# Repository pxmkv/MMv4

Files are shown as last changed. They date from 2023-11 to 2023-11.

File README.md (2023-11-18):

# MMv4

MMv4 is the 4rd generation robot platform used to teach the IEEE Micromouse DeCal at UC Berkeley. It was designed with usability, manufacturability, size, and cost in mind.

## Setup

1. Follow the assembly instructions in [lab1](docs/lab1.md) using the latest **BOM**.
2. Plug mouse into your computer and flash the Micropython firmware

## Labs

Skeleton lab code, lab documents, and solutions are stored in [labs/](labs/), [docs/](docs/), and [solutions/](solutions/), respectively. To get started with a lab, simply copy the contents of the folder over to the MicroPython drive and edit files from there.

* [sanity](docs/sanity.md) - Hardware Check
* [lab1](docs/lab1.md) - Assembly
* [lab2](docs/lab2.md) - MicroPython Basics
* [lab3](docs/lab3.md) - Encoders
* [lab4](docs/lab4.md) - IR Sensors and Gyroscope
* [lab5](docs/lab5.md) - Odometry, Gyroscope and Motor Control
* [lab6](docs/lab6.md) - Intro to PID
* [lab7](docs/lab7.md) - More PID
* [lab8](docs/lab8.md) - Maze Solving Primitives **(WIP)**

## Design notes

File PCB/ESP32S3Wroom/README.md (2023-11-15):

## This folder contains all design files of Micromouse with ESP32S3Wroom as MCU

**Software Used**
1. Altium Designer 22
2. AutoCAD 2022

**Parameter**
1. Vias hole size: 12mil~15mil
2. Vias diameter: 20mil~30mil
3. Tracks width: 10mil~30mil
4. Layers: 2 layers
5. Silkscreen width: 10mil
6. Copper thickness: 1oz

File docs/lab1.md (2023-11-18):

# Lab 1: CircuitPython Basics

## CircuitPython Basics

One of the most convenient features of CircuitPython is the ability to upload and modify code as if they were just files on a flash drive. Instead of editing code directly on the drive, we highly recommend **editing code locally** on your computer first and then copying it over to the drive to run. This reduces wear on the flash memory and ensures you have a local backup of your code.

On startup, CircuitPython looks for a file named `code.py` and runs it. There are a few differences, but for the most part it behaves just like normal Python. After uploading new code, you might need to bring up a serial monitor and press CTRL-C and CTRL-D to reload.

For debugging, the serial monitor is invaluable. This is where the output of `print` statements will go. You can even bring up a REPL. One important note is that you can't start an interactive session (e.g. `python -i code.py`) to further debug your code as CircuitPython will restart on entering one.

### Example 1: Blinky

Let's start with the blink example, the "Hello World" of embedded programming. Your mouse has a green LED on the Pi Pico and an onboard WS2812B NeoPixel RGB LED. Upload the following code to your mouse.

```python
import board     # pin definitions
import time      # time delay
import neopixel  # to control the WS2812B
import digitalio # to control the LED

print("Hello World!")

# setup the LED as an output
led = digitalio.DigitalInOut(board.LED)
led.direction = digitalio.Direction.OUTPUT

# setup the WS2812B
rgb = neopixel.NeoPixel(board.GP4, 1)

# blink
while True:
    rgb[0] = (255, 255, 255) # max brightness
    led.value = True
    time.sleep(0.5)
    rgb[0] = (0, 0, 0)
    led.value = False
    time.sleep(0.5)
```

Running the code, both LEDs should start blinking every 0.5s. Notice that before we start writing values to the LEDs, we need to set them up with the correct physical pin. Also, WS2812Bs can be chained into strings which is why we use `rgb[0]`, to address the first (and only) LED.

### Checkoff #1

1. Change something about the provided blink code such as RGB color and blink rate.

### Example 2: Unnecessarily Complex Blinky

Let's take a look at some more syntax. Upload the following code to your mouse.

```python
import board
import time
import neopixel

rgb = neopixel.NeoPixel(board.GP4, 1)

counter = 0
while True:
    counter += 1
    if counter % 5 == 0: # modulus a.k.a remainder
        rgb[0] = (100, 0, 0)
        time.sleep(0.5)
        rgb[0] = (0, 0, 0)
    else:
        for i in range(5): # 0, 1, 2, 3, 4
            time.sleep(0.1)
```

Here we introduce a couple programming constructs that are very common in coding. The `if` statement (pairable with `elif` and `else`) runs the block of code corresponding to the truthiness of what's next to the `if`. The `for` loop sequentially iterates through an object which in this case is `range(5)`.

### Checkoff #2

1. What is the blink pattern? How long is it on and off for?

### Example 3: 

Finally, let's test out the button on your mouse. It's connected to pin `GP3`. Fill in the TODOs below to have your RGB LED change color when the button is pressed.

```python
import board
import time
import neopixel
import digitalio

rgb = neopixel.NeoPixel(board.GP4, 1)

but = digitalio.DigitalInOut("""TODO which pin?""")
but.pull = digitalio.Pull.UP

while True:
    if but.value: # not pressed
        """TODO one color"""
    else: # pressed
        """TODO other color"""
```

### Checkoff #3

1. Demonstrate your working code.

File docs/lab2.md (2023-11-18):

# Lab 2: Assembly

PLUG YOUR PI PICO INTO YOUR COMPUTER BEFORE YOU SOLDER IT JUST TO MAKE SURE IT WORKS :D

## Assembly

Download the `ibom.html` from the [release](https://github.com/dragonlock2/MMv3/releases) that matches your board revision and open it in your preferred browser. The interactive BOM (bill of materials) shows what parts are needed on your mouse's PCB (printed circuit board) and where they need to be placed.

To see images of all parts, see the Google Drive link [here](https://drive.google.com/drive/folders/1rGae82BSrE_mvmMwKTBHT9P-unDKIKQj?usp=sharing).

Also check the latest release for any manufacturing notes to make an older board functionally equivalent to the newest revision.

### Reflow Soldering

Let's start with the back of the PCB which is where the majority of parts are located. Click `B` in the top right to show just the back.

<p align="center">
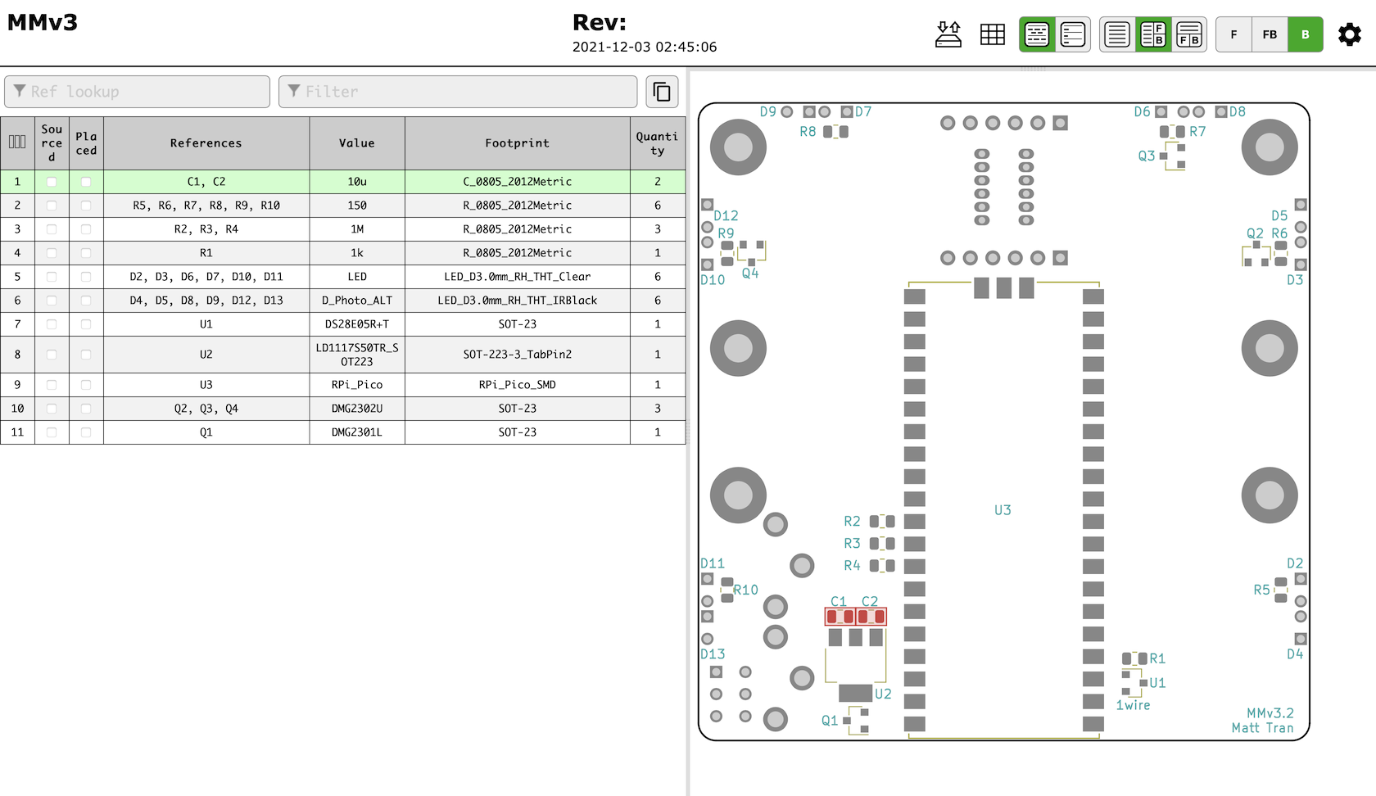
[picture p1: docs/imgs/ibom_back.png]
    
    <br>
    <a><b>iBOM Back</b></a>
</p>

Rather than solder each part by hand, we'll use reflow soldering which does it all at once. In reflow soldering, we place components on top of pads covered in solder paste before sending the whole thing through an oven to melt the solder, making permanent joints.

<p align="center">
    
    <br>
    <a><b>Reflow Solder Process</b></a>
</p>

Let's start by applying the solder paste using a **solder stencil**. Instead of squeezing the perfect amount onto each pad by hand, we can do it all at once by spreading paste over a stencil with holes cut out precisely where we want paste. For a good solder paste application, it's important to make sure the stencil is flush against the PCB and stays aligned. The process is very forgiving, so don't worry if your paste looks messy or goes a bit outside the pads.

<p align="center">
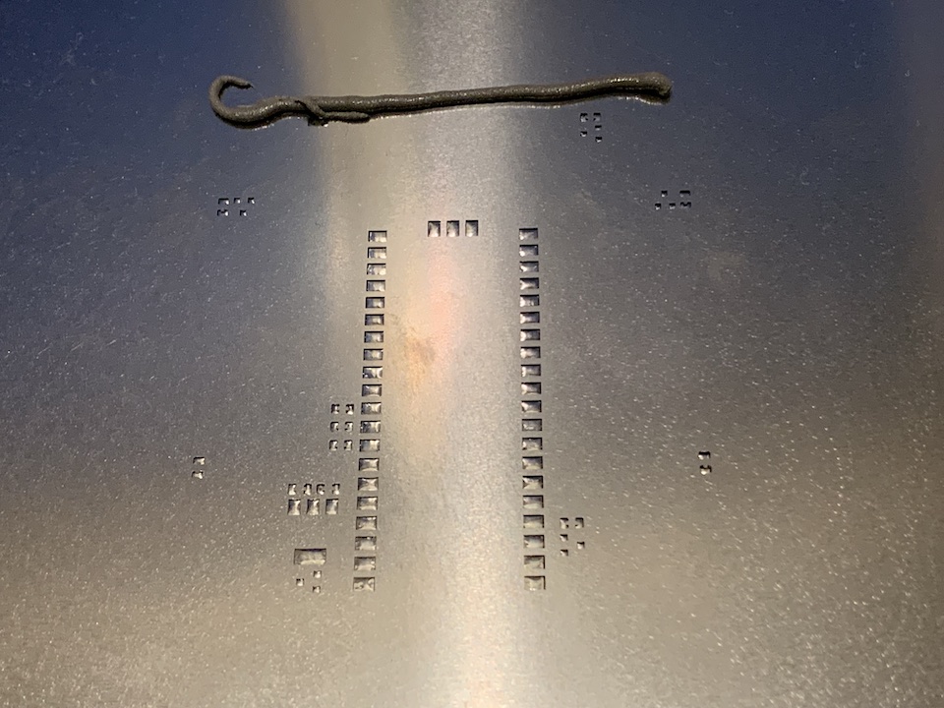
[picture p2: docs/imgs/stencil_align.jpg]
    
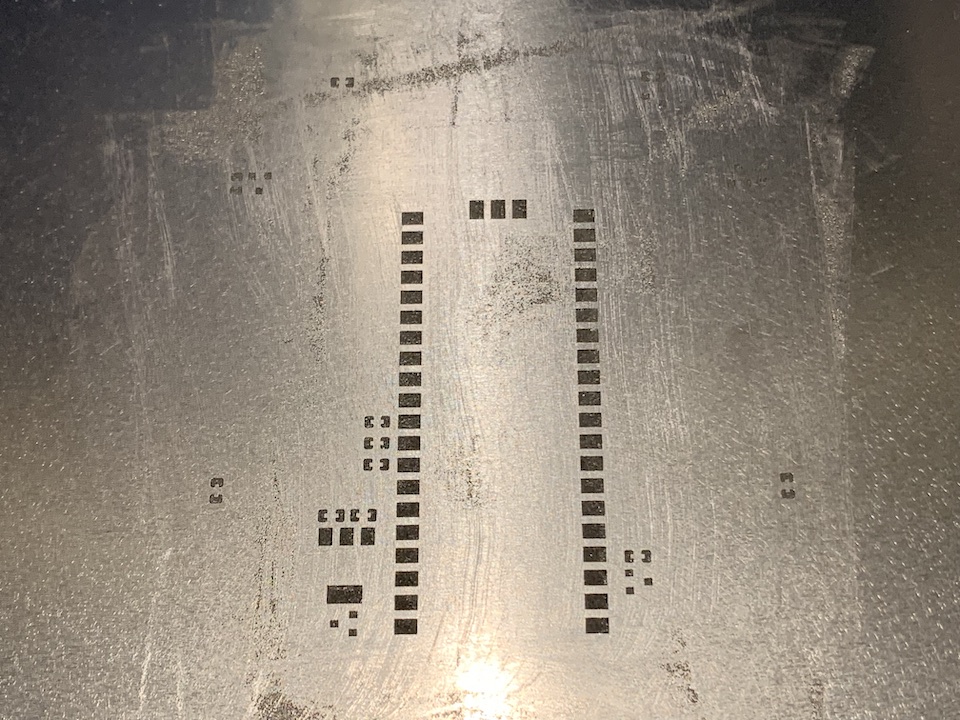
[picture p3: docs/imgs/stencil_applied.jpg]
    
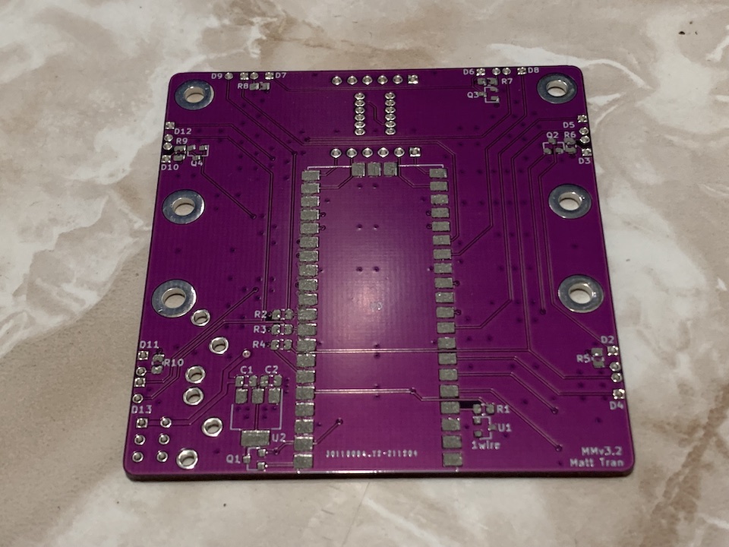
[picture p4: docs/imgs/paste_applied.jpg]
    
    <br>
    <a><b>Solder Paste Application Process</b></a>
</p>

Now it's time for component placement. Following the `ibom.html`, place all of the components for the back side. None of the symmetric components have polarity, so don't worry about part orientation. Tweezers will be very useful, but don't squeeze too hard or your component will go flying. When placing components, press down gently so that it digs into the paste a bit to prevent it from moving. Again, the process is quite forgiving so don't worry if your parts aren't perfectly aligned as solder surface tension will generally pull them into alignment.

<p align="center">
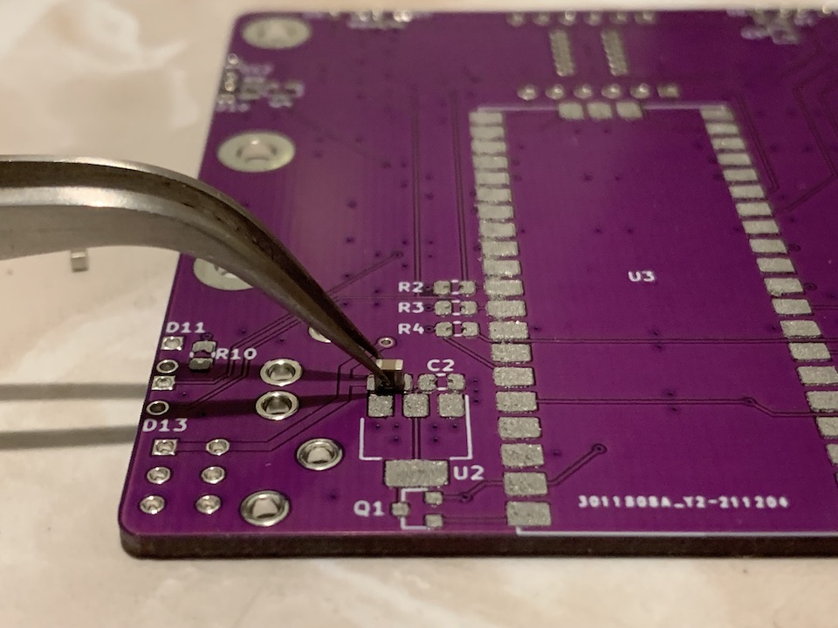
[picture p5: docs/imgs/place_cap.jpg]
    
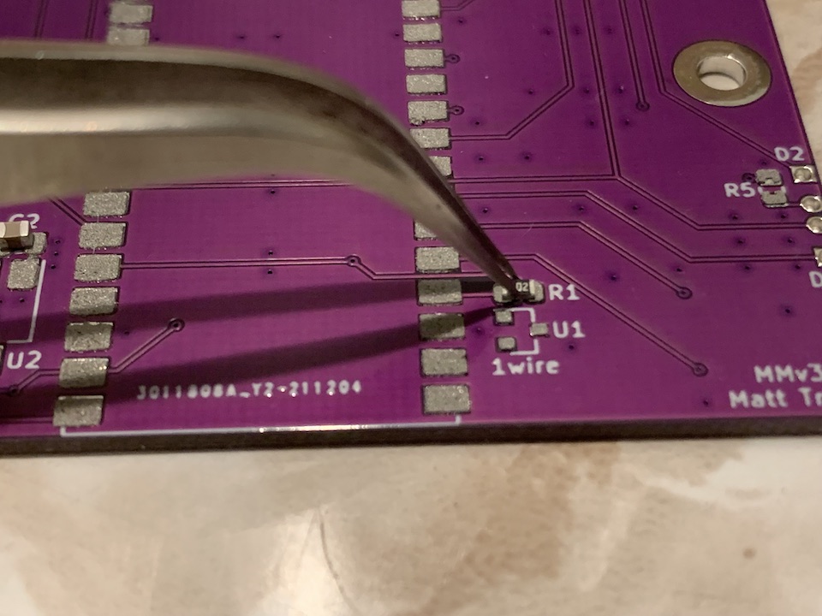
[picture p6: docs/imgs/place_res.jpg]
    
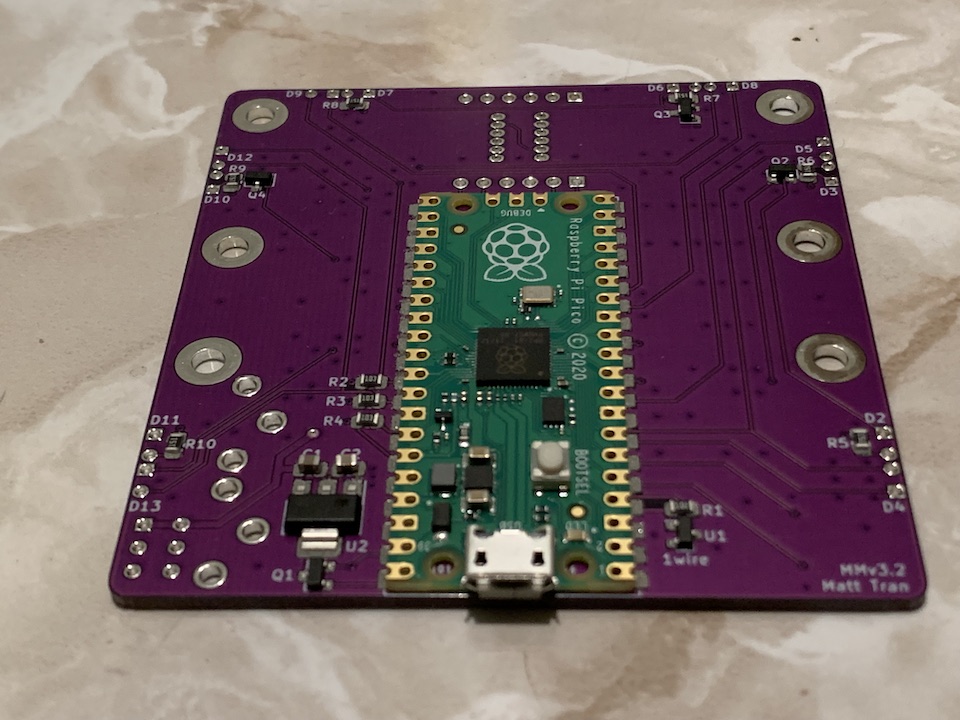
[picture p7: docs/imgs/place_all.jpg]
    
    <br>
    <a><b>Component Placement</b></a>
</p>

Finally, let's reflow the solder! Throw your board into the reflow oven, load up the correct profile, and wait. With any luck, all of your joints will melt and the back side of your board will be done.

<p align="center">
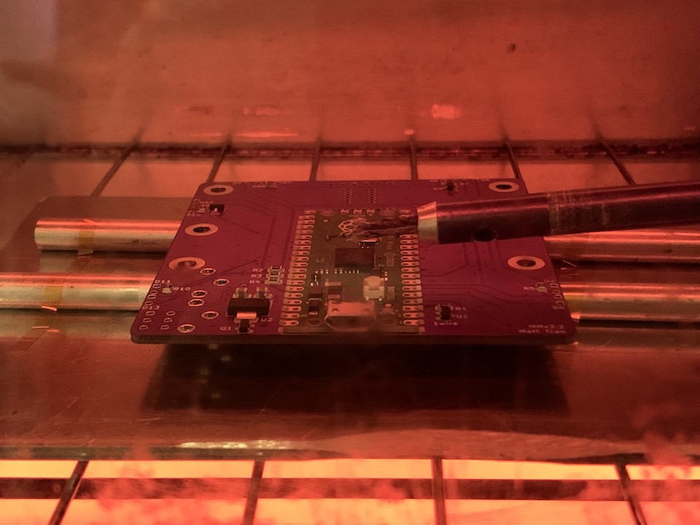
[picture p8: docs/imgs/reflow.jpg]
    
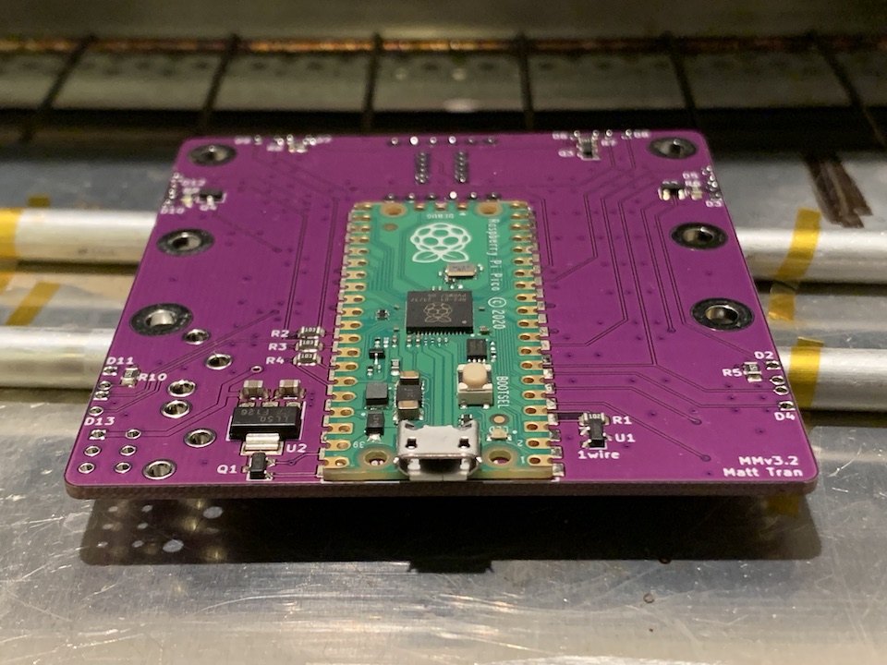
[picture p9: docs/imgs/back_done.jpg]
    
    <br>
    <a><b>Reflow</b></a>
</p>

### Hand Soldering

The rest of the components need to be attached by hand. The general process is to heat up both the pad and the part before melting solder onto both of them. Adafruit has a great list of common issues and fixes which can be found [here](https://learn.adafruit.com/adafruit-guide-excellent-soldering/common-problems).  

<p align="center">
    
    <br>
    <a><b>How to Make a Solder Joint</b></a>
</p>

Let's start with the DRV8833 motor driver board. Solder the two 6-pin headers onto the board and bridge the `en` pads as shown in the following pictures. The technique that I find works best is to solder just one pin first with the part in any orientation. Then reheat that joint while pressing on the part to move it into perfect alignment. Finally, do the rest of the pins.

<p align="center">
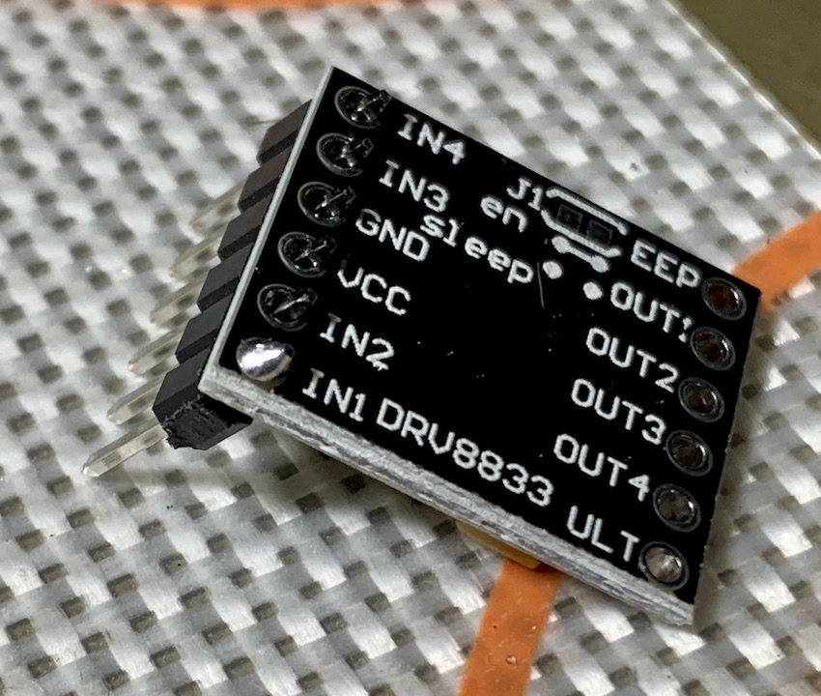
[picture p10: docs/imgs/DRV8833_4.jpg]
    
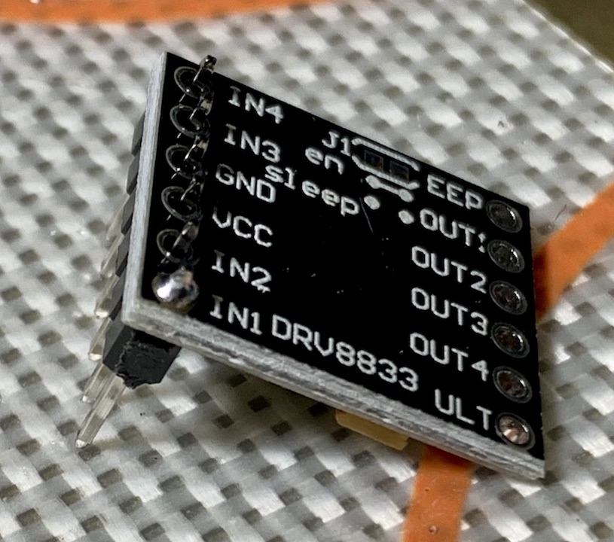
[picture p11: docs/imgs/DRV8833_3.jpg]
    
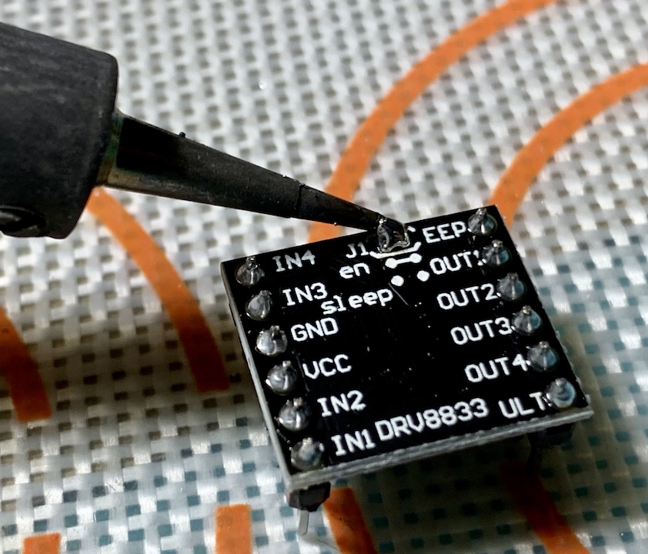
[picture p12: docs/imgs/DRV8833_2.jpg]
    
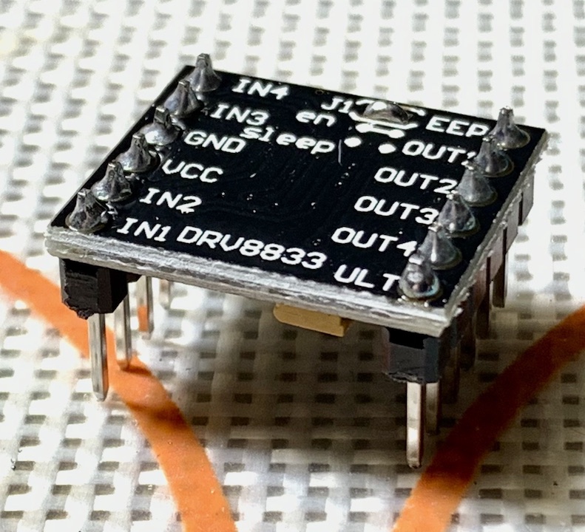
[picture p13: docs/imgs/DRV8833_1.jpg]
    
    <br>
    <a><b>DRV8833 Motor Driver Assembly</b></a>
</p>

Next let's finish off the mouse's main PCB. Click `F` in the `ibom.html` to see the remaining components.

<p align="center">
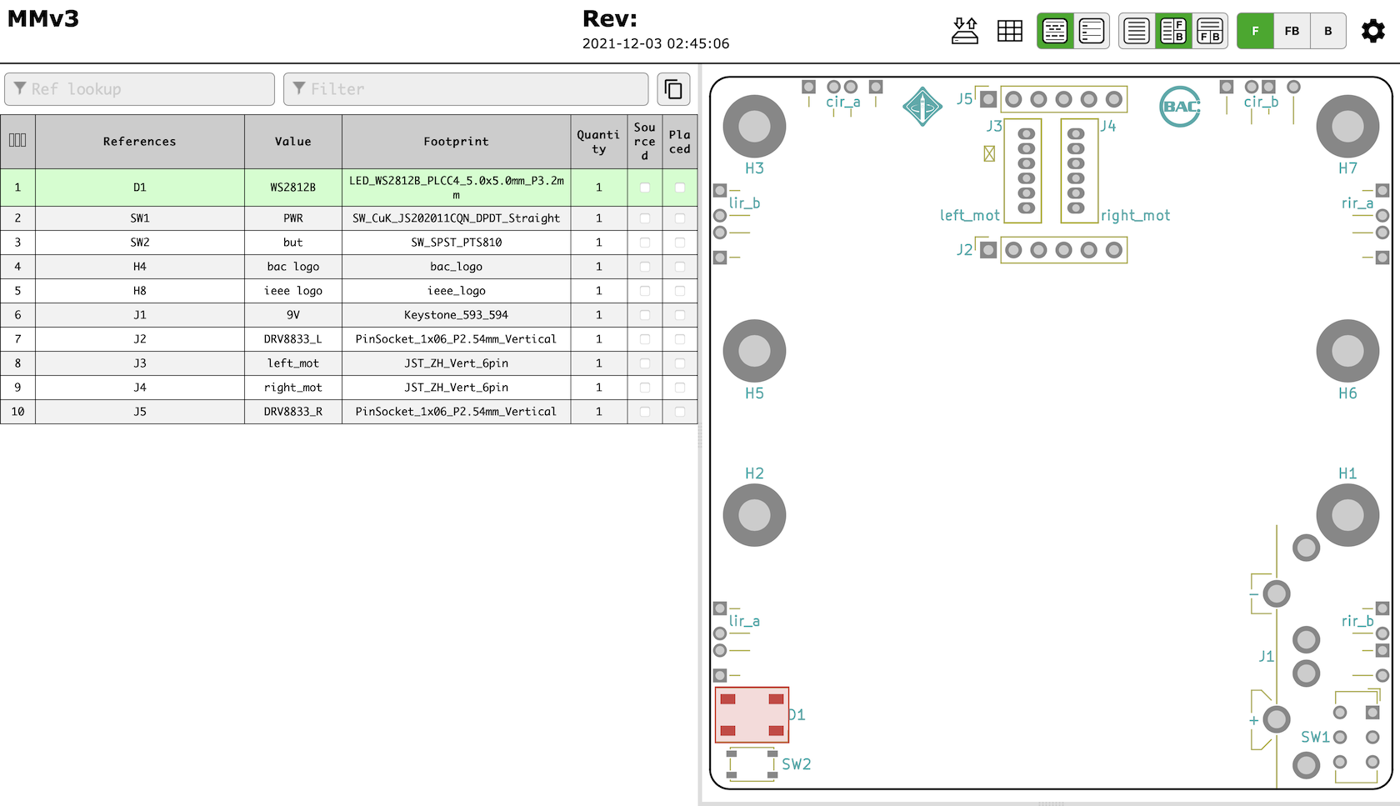
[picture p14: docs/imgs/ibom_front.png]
    
    <br>
    <a><b>iBOM Front</b></a>
</p>

To make alignment easier, starting with the shortest components usually works out best. The SMD components use the same soldering process except there's no hole to stick the part through. Some of the parts do have polarity, so if you're unsure make sure to ask your mentor.

<p align="center">
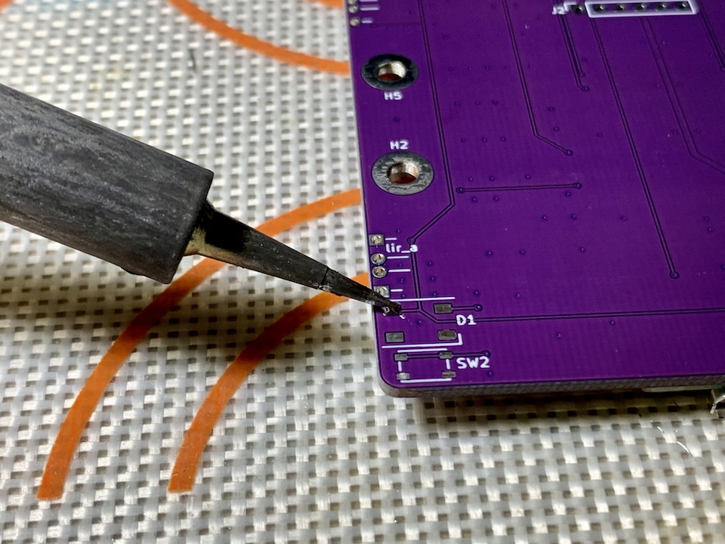
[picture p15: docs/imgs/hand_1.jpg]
    
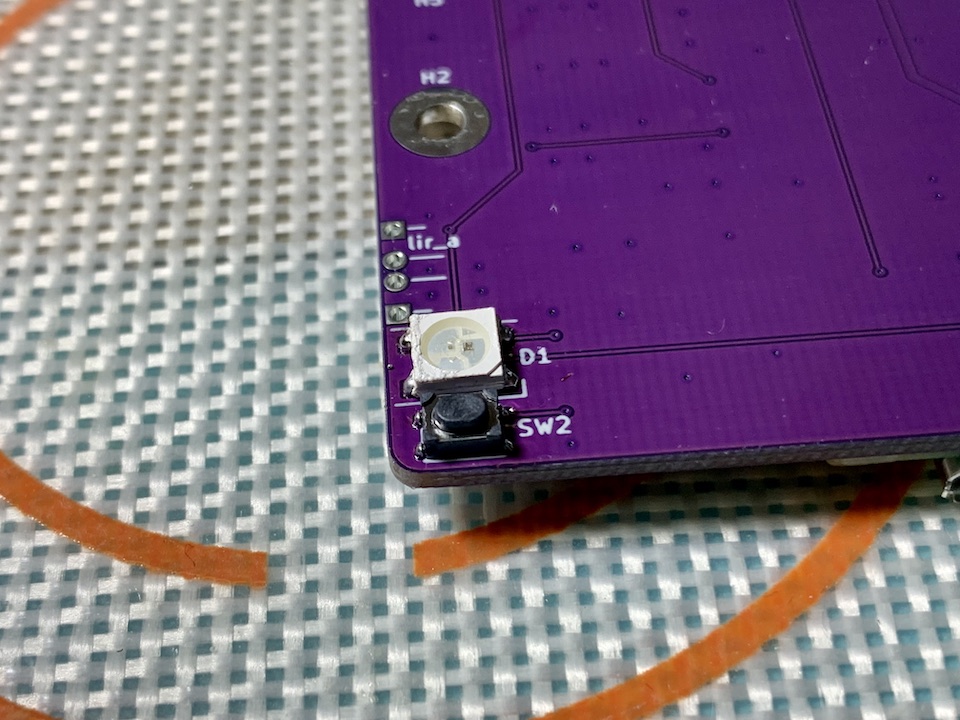
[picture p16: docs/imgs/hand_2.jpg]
    
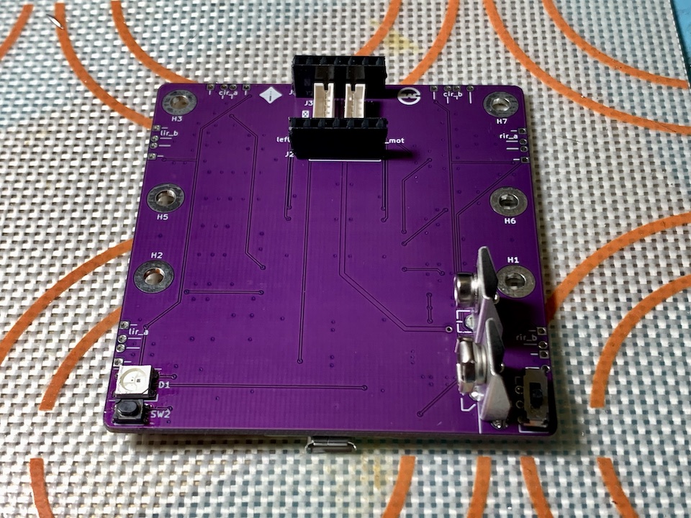
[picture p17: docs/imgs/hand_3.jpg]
    
    <br>
    <a><b>Some THT Components</b></a>
</p>

For the IR LEDs, the silkscreen should denote the polarity. They also need to be mounted at a right angle so don't be afraid to bend them. Splaying the leads outward should hold them in place while you apply solder.

<p align="center">
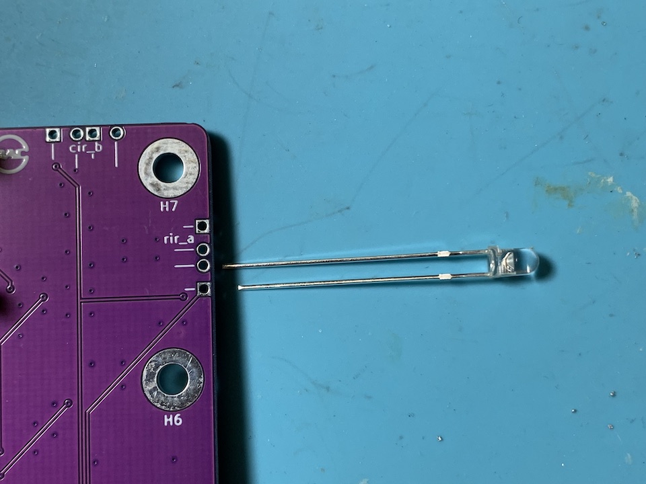
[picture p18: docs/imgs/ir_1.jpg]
    
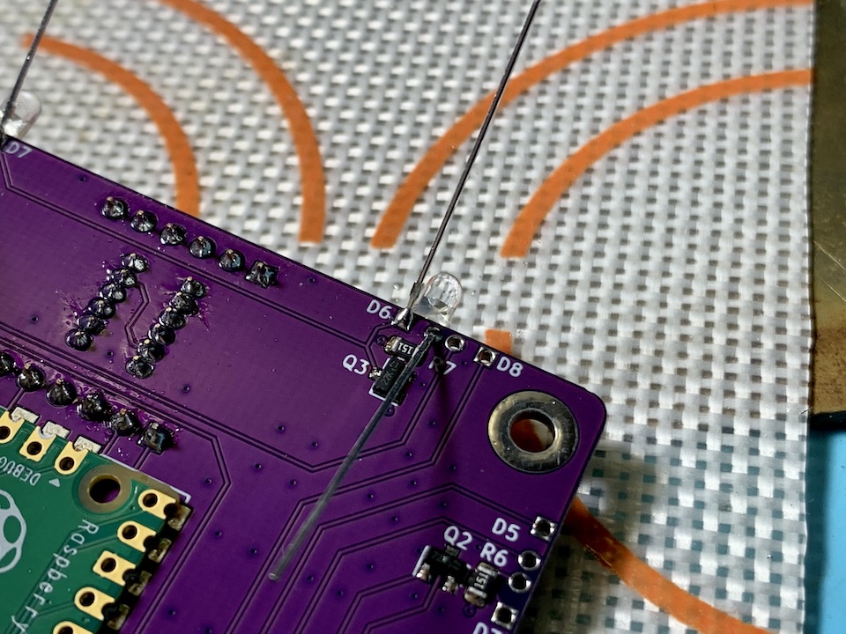
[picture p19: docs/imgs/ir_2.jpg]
    
    <br>
    <a><b>IR LEDs</b></a>
</p>

With any luck, your board should be finished!

<p align="center">
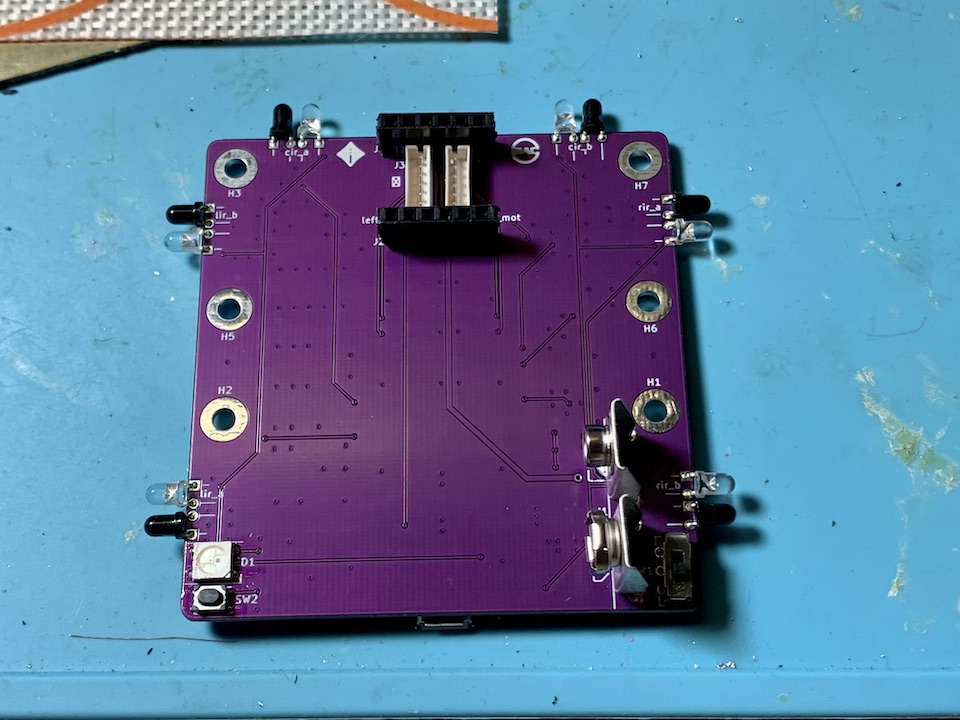
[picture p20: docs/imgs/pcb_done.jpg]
    
    <br>
    <a><b>Assembled PCB</b></a>
</p>

### Mechanical Assembly

Let's finish assembling the mouse. Follow the pictures below. The screw threads are printed into the plastic so don't overtighten them. Don't be afraid to apply a bit of force when attaching the wheels since a tighter fit improves concentricity.

<p align="center">
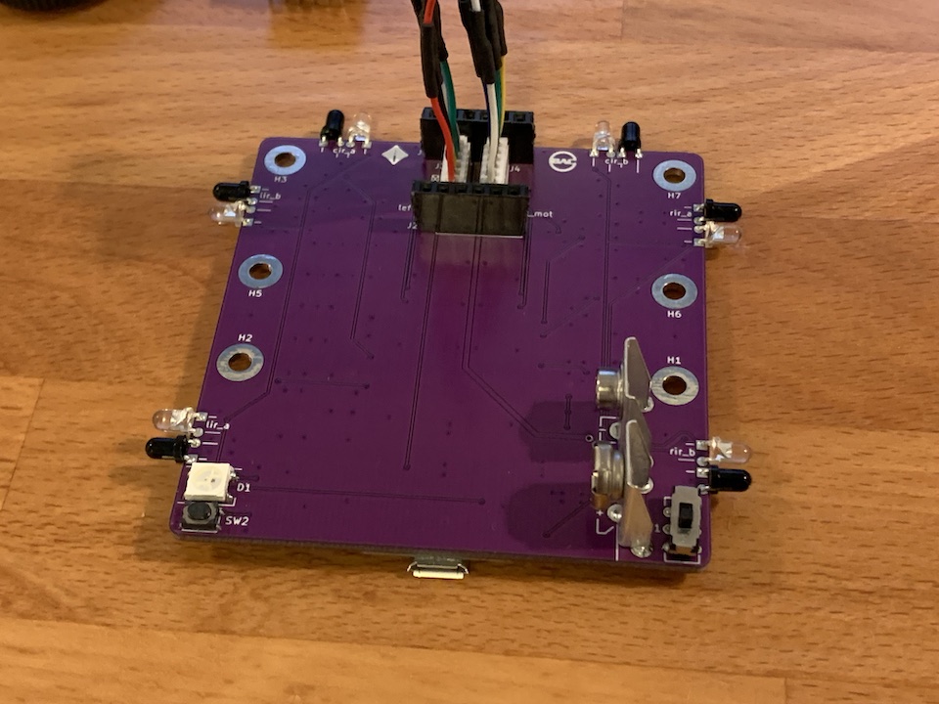
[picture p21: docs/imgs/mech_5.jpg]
    
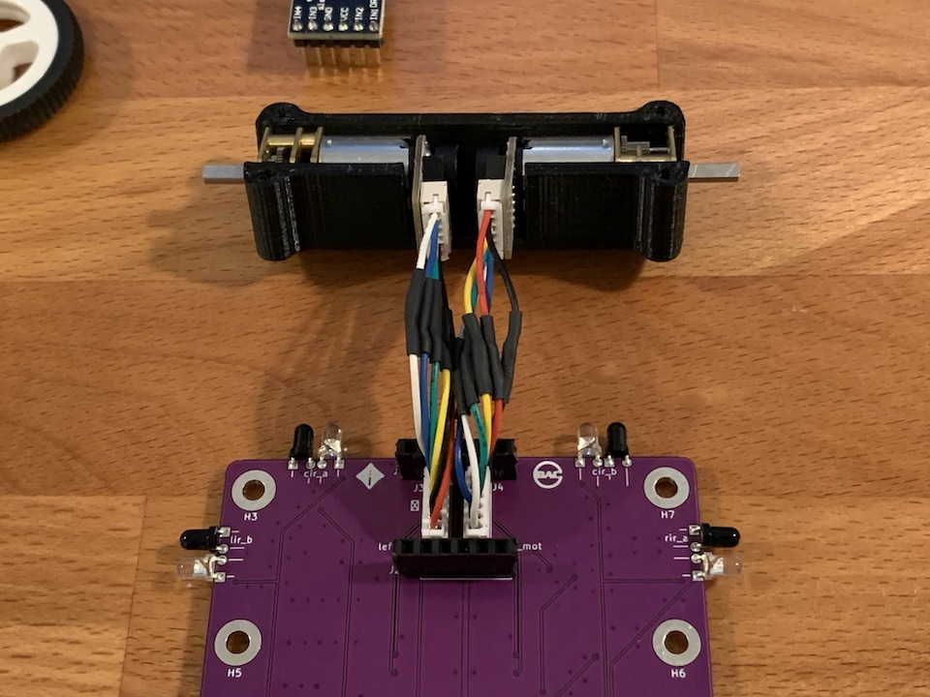
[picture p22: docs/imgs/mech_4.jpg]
    
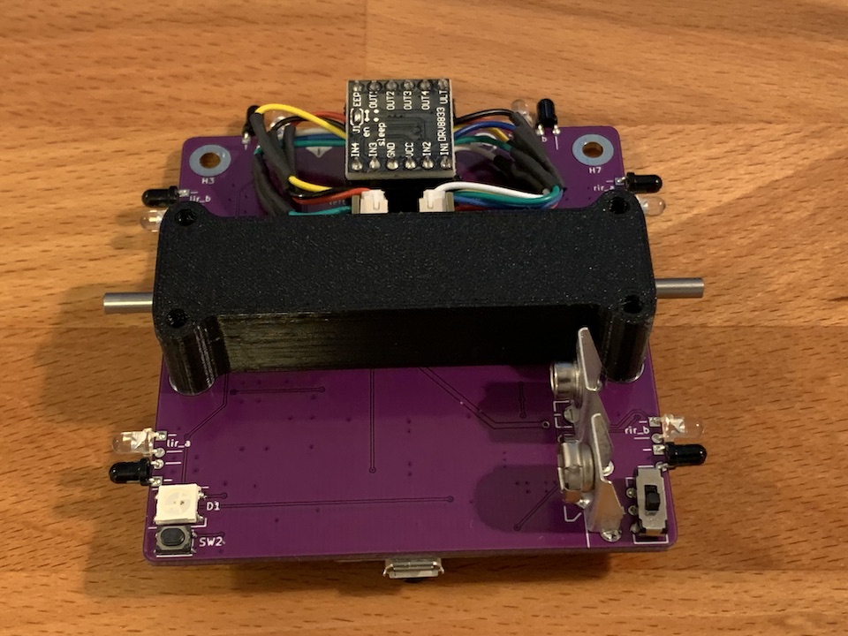
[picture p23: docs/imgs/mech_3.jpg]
    
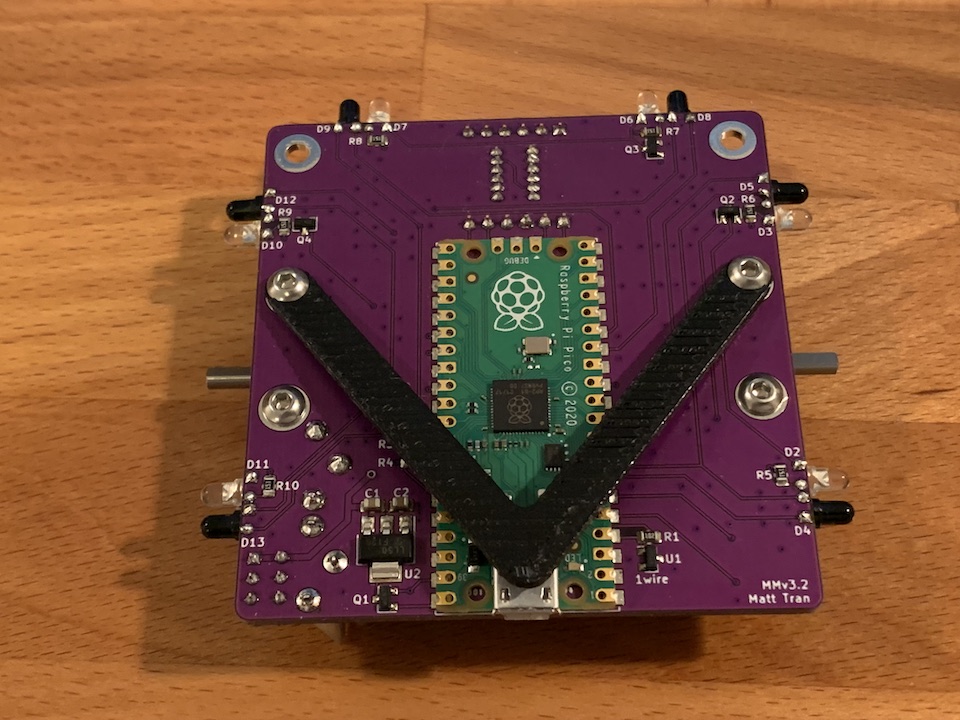
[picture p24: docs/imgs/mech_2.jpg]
    
    
    <br>
    <a><b>Final Assembly</b></a>
</p>

## Sanity Check

Now that your mouse is assembled, it is time to run a sanity check to make sure everything is working.

1. Follow the [setup](../README.md) instructions to get the firmware and libraries uploaded.
2. Follow the [sanity lab](sanity.md) to run the sanity check.

## IR Calibration

If you placed your mouse against a reflective surface, you may have noticed that the IR readings change. Since our sensors are currently mounted perpendicular to the mouse, they pick up some reflection from the surface the mouse sits on. To fix this, we're going to bend our IR sensors ever so slightly upwards to compensate.

Bring up the sanity check again to the IR sensor printout section. Bend your IR sensors upwards just enough so that the difference between pointing them into free space and placing them on a surface is less than 2,000.

<p align="center">
    
    <br>
    <a><b>Bent IR Sensors</b></a>
</p>

### Checkoff #1

1. Show your mentor your assembled mouse, passing sanity check, and calibrated IR sensors.

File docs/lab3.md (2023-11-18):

# Lab 3: Encoders

## Background

When we're navigating the maze, we'd like to keep track of a couple things.

* Is it driving straight?
* How far has it driven?
* What direction is it facing?

To answer these questions, we'll use the **quadrature encoder** sensors mounted on the back of your motors. They consist of a spinning magnet and two Hall effect sensors mounted 90° apart. Hall effect sensors measure the presence of magnetic fields. In our case, they output a `True` when closer to a north pole and `False` when closer to a south pole.

<p align="center">
    
    <br>
    <a><b>Hall sensor signal (y-axis) vs. time (x-axis)</b></a>
</p>

## Waveform Viewing

Let's try reading raw values from the encoder. Upload the following code.

```python
import board
import time
import digitalio

# left encoder
a = digitalio.DigitalInOut(board.GP12)
b = digitalio.DigitalInOut(board.GP13)

while True:
    print(int(a.value), int(b.value))
    time.sleep(0.001)
```

Pull up a serial monitor and start spinning the left motor at various speeds. Notice how the values start changing. Can you tell which direction the motor is spinning with just one input?

### Checkoff #1

1. What's the output when the motor is stationary? Is it a certain level? Is it constant?
2. How does the output change when you spin the motor faster?
3. Why do we need two Hall effect sensors per motor?

## Polling

Next let's try tracking the position of the left wheel. We're going to use a technique called polling which involves repeatedly reading a signal to detect changes. Fill in the `leftEncoderRisingEdge` function below.

```python
import board
import digitalio

# left encoder
a = digitalio.DigitalInOut(board.GP12)
b = digitalio.DigitalInOut(board.GP13)

counter = 0
position = 0
a_prev = a.value

def leftEncoderRisingEdge():
    global position # access global position
    """TODO increment or decrement position"""

while True:
    a_val = a.value
    if a_val and not a_prev: # rising edge
        leftEncoderRisingEdge()
    a_prev = a_val

    if counter % 1000 == 0:
        print(position)
    counter += 1
```

After uploading the code, pull up a serial monitor and start spinning the motor in both directions. The position should go up and down as you do it!

### Checkoff #2

1. Show your working code.
2. Roughly how many "ticks" correspond to a revolution? How do you think this is computed?
3. What issues might the "polling" method have?
4. Now that we can measure position, how might we measure velocity?
5. What effect does swapping the A and B pins have on how we measure position?

## Interrupts

Polling can be inefficient and even miss edges if the wheel is spinning too quickly. Moreover, constantly having to check a signal takes up a lot of CPU time that could be used for other purposes. While polling is adequate in some cases, for an encoder we need something better.

Interrupts literally interrupt the CPU by making it pause its current task and run some other code before resuming. In our case, we want to trigger an interrupt when a pin has a rising edge. The low-level setup for interrupts usually involves enabling some registers and assigning a function to run. CircuitPython actually abstracts all of this away for us in the `rotaryio` module.

Upload the following code.

```python
import board
import time
import rotaryio

enc = rotaryio.IncrementalEncoder(board.GP12, board.GP13)

while True:
    print(enc.position)
    time.sleep(0.001)
```

Pull up a serial monitor and start spinning the motor.

### Checkoff #3

1. Demonstrate the working code.
2. Why might we use interrupts over polling?

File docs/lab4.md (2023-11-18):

# Lab 4: IR Sensors

## Background

IR sensors work by sending out IR light and measuring the amount reflected back. They take a lot more work to calibrate and are surface dependent, but are far cheaper and faster than the ToF sensors we used to use. Our mouse has 6 of these sensors split into 3 pairs (center/front, left, right). Having 2 sensors per side allows us to statically determine both the distance and angle of the nearest surface.

IR sensors consist of both an IR emitter and detector. IR emitters draw around 50mA each when on, so we have a switch to turn them off when not needed. IR detectors shift their IV curve based on light intensity like in the following graph.

<p align="center">
    
</p>

To convert that to a readable voltage signal, we'll use a setup similar to a resistor divider. It's noisier and less tunable compared to a transimpedance amplifier, but uses only one resistor. By placing the IR detector in reverse bias, we use the flatter region of the IV curve. Since the current varies linearly with light intensity, the voltage also varies linearly. MMv3 uses the following circuit (pull-up resistor not shown).

<p align="center">
    
</p>

## Read One Sensor

Since we have 6 total analog sensors but only 3 ADC pins on the Pi Pico, we need to multiplex 2 sensors onto each pin. We use one extra pin on each IR detector in open-drain mode to fully disconnect or connect it to ground. To read in one sensor, we perform the following steps.

1. Enable the IR emitters (set pin to `True`).
2. Enable the chosen sensor by connecting it to ground (set pin to `False`).
3. Wait around 1ms for things to settle.
4. Take the reading.
5. Disable the chosen sensor by setting the pin to open-drain (set pin to `True`).
6. Disable the IR emitters (set pin to `False`).

Baesd on the above steps and the `AnalogIn` [documentation](https://circuitpython.readthedocs.io/en/latest/shared-bindings/analogio/index.html), fill out the below TODOs to print out readings from the left IR sensor pair (`lir_a` and `lir_b`).

```python
import board
import time
import digitalio
from analogio import AnalogIn

l_en  = """TODO create DigitalInOut output on GP7"""
l_adc = """TODO create AnalogIn on GP28"""

l_a   = digitalio.DigitalInOut(board.GP5)
l_a.direction  = digitalio.Direction.OUTPUT
l_a.drive_mode = digitalio.DriveMode.OPEN_DRAIN
l_a.value = True # high Z mode

l_b = """TODO create DigitalInOut on GP6 in open-drain mode"""

while True:
    # TODO enable IR emitters using l_en
    # TODO enable chosen sensor l_a or l_b
    # TODO wait a bit
    # TODO take analog reading for future printing
    # TODO disable chosen sensor l_a or l_b
    # TODO disable IR emitters using l_en
    time.sleep(0.05)
```

### Checkoff #1

1. Demonstrate one working sensor.

## Read All the Sensors

In order to simplify the whole process of multiplexing and reading from multiple sensors, we wrote a library. Upload `irsensor.py` from [sanity/](../labs/sanity) to serve as the library. Read through `irsensor.py` to instantiate and use it and fill out the below TODOs to print out all sensor readings in real time.

```python
import board
import time

from irsensor import IRSensors

ir = IRSensors(
    """TODO sensor | en   | a    | b    | adc"""
    """TODO lir    | GP7  | GP5  | GP6  | GP28"""
    """TODO cir    | GP9  | GP10 | GP11 | GP26"""
    """TODO rir    | GP21 | GP20 | GP22 | GP27"""
)

while True:
    """TODO get and print all sensor readings"""
    time.sleep(0.05)
```

### Checkoff #2

1. Demonstrate all of your working sensors.

## Calibration

Let's try estimating actual distances from the sensor values. Empirically, the relationship is linear below around 60mm and rises sharply beyond that due to the angled sensors seeing above the wall. Based on maze cell size, we really only need accurate distances around 50mm for wall following and just binary wall detection beyond that.

<p align="center">
    
    <br>
    <a><b>IR Sensor Linear Region</b></a>
</p>

Load up [`code.py`](../labs/lab4/code.py) which contains code to automate finding the constants. You'll be using a maze wall and ruler to take readings at various distances. The code then uses least squares to fit a line to the points and prints out the constants at the end. The equation using these constants to convert sensor readings to distances can be expressed as follows.

<p align="center">
    $distance = a \cdot sensor + b$
</p>

### Checkoff #3

1. Run the calibration code and save the constants somewhere.
2. Using the constants, write code to convert sensor values to distances.

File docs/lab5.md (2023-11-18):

# Lab 5: Odometry and Motor Control

## Background

### Odometry

Now that we know how to read the encoders on our mouse, we can use that to estimate the position and orientation of our mouse at any given time. This is a form of *odometry*.

Why is odometry important? Suppose we want our mouse to move forward by one maze cell. We could turn on both motors for a fixed amount of time, and hope the mouse moves exactly the distance we want it to. In practice, this doesn’t work due to friction, changing battery voltage, and many other factors. The difference between the desired movement and the actual movement is called *error*, and knowing the error is the first step towards correcting it.

Using the measurements from both wheels, we can compute the odometry for the entire mouse. Our mouse is a *differential drive* robot, which means that it has two drive wheels located side by side. Both wheels turning in the same direction causes forward (or backward) motion, and both wheels turning in opposite directions causes rotation.

When we describe the position and velocity of a robot, we are actually describing the position and velocity of a single point somewhere on the robot. For a differential drive robot like our mouse, this point is usually taken to be halfway between the wheels. Since a point can’t have a rotational velocity, the “point” is actually a *coordinate frame*. You can think of a coordinate frame as a set of coordinate axes that are “attached” to the mouse and move/rotate with it.

<p align="center">
    
</p>

Consider the coordinate frame in the diagram above. When the mouse moves forward, it moves in the positive x direction. When the mouse rotates, it rotates around the z axis (which points upwards). The concept of coordinate frames is fundamental to robotics, but we won’t be able to cover it in much depth (try EECS C106A if you're interested in this type of stuff!). Fortunately, we only need to know some basics.

<p align="center">
    
</p>

We are mostly interested in the forward distance and rotational distance of our mouse. Intuitively, the center of the mouse moves with a distance that is the average of the wheel distances. Rotation in radians is arc distance divided by diameter which in our case would be the difference in wheel distances divided by the distance between the wheels. We can derive the following formulas.

<p align="center">
    $d_f = \frac{d_l + d_r}{2}$
    <br>
    $\theta = \frac{d_r - d_l}{d}$
</p>

### Motor Control

To make the mouse move, we use brushed DC motors. Applying a voltage across them makes the motor spin in one direction. Reversing this voltage makes the motor spin in the other direction.

Motors need large amounts of current and as such our Pi Pico can't drive them directly from its IO like we could with the LEDs. To solve this problem, we use the DRV8833 motor driver chip. It can drive two small motors and includes features like overcurrent protection and PWM control.

<p align="center">
    
</p>

Above is the DRV8833 breakout board we use in our mouse. One of the motors is connected to the OUT1 and OUT2 pins while the other is connected to the OUT3 and OUT4 pins. The Pi Pico is connected to the INx pins to allow it to control the corresponding OUTx pins.

Since the DRV8833 is a high power device, it needs to be powered off the 9V lithium battery included with your mouse. When using the motors, turn on the switch on your mouse to connect the battery.

To control the motors, we can reference the [datasheet](https://www.ti.com/lit/ds/symlink/drv8833.pdf). The relevant section is copied below for convenience.

<p align="center">
    
</p>

`1` means setting a pin to `True` while `0` means setting it to `False`. `Z` means the pin is "disconnected" which is also known as high impedance mode. Since we power the DRV8833 with 9V, `H` means 9V and `L` means 0V.

## Odometry

Translate the odometry equations into code by filling in the TODOs in the below code. Note that you'll first have to convert the number of encoder ticks to the actual distance traveled.

```python
import board
import time
import rotaryio
from math import pi

lenc = rotaryio.IncrementalEncoder(board.GP12, board.GP13)
renc = rotaryio.IncrementalEncoder(board.GP19, board.GP18)

ENCODER_TICKS_PER_REVOLUTION = """TODO from previous lab"""
WHEELBASE_DIAMETER = """TODO measure this in mm"""
WHEEL_DIAMETER = 34.0 # mm

while True:
    left_dist  = """TODO"""
    right_dist = """TODO"""

    dist  = """TODO"""
    theta = """TODO"""

    print(dist, theta)
    time.sleep(0.05)

```

### Checkoff #1

1. Demonstrate your working code.
2. How many millimeters does a wheel travel per encoder tick?

## Motor Control

Based on the table from the datasheet, the DRV8833 can easily put motors in forward or reverse at full power and even stop. What if we want to use a different speed? To do this we can switch between full power and stop really quickly so that we average out somewhere in between based on the proportion of time we spend in each. This is the main idea behind PWM (Pulse Width Modulation).

CircuitPython has a builtin module for this called `pwmio`. Documentation for it can be located [here](https://circuitpython.readthedocs.io/en/latest/shared-bindings/pwmio/index.html). The important values in PWM are duty cycle and frequency. Duty cycle determines the percentage of time within a cycle spent on. In the case of `pwmio`, it's a 16-bit number (0-65535). Frequency is determined by the total of the on and off times and is specified in Hertz. Since frequency determines the noise, we'll keep it at 20kHz to be at the edge of human hearing.

Look at the `pwmio` documentation and fill in the TODOs below. A duty cycle of 0 or 65535 will set a pin to be completely off or on, respectively. For reasons best explained in a nice [article](https://learn.adafruit.com/improve-brushed-dc-motor-performance/choosing-decay-mode-and-pwm-frequency), we want to switch between the forward and slow decay states of the DRV8833 for PWM.

```python
import board
import pwmio

lmot_in1 = """TODO create PWMOut object on pin GP16 at 20kHz"""
lmot_in2 = """TODO create PWMOut object on pin GP17 at 20kHz"""

while True:
    lmot_in1.duty_cycle = """TODO set to 25% speed forward"""
    lmot_in2.duty_cycle = """TODO set to 25% speed forward"""
```

### Checkoff #2

1. Demonstrate your left wheel spinning forward at 25% speed.
2. What happens if we swap the two PWM pins?

## Motor Control w/ Library

Having to deal with PWM outputs and duty cycles can get tedious. As is usually the case, CircuitPython provides a nice library named `motor` for this very thing. Read the [documentation](https://circuitpython.readthedocs.io/projects/motor/en/latest/api.html) and fill out the TODOs in the following code.

```python
import board
import time
import pwmio
import adafruit_motor.motor as motor

"""TODO don't forget to make PWMOut objects first"""

lmot = """TODO create DCMotor object on pins GP16 and GP17"""
rmot = """TODO create DCMotor object on pins GP15 and GP14""" 

"""TODO set lmot and rmot to SLOW_DECAY"""

while True:
    """TODO move full speed forward for 1s"""

    """TODO brake for 1s"""

    """TODO move 25% speed backward for 1s"""

    """TODO brake for 1s"""
```

### Checkoff #3

1. Demonstrate your code is working.
2. What happens if we pass a `throttle` value larger than 1.0 or -1.0?

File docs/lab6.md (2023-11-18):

# Lab 6: Intro to PID

## Background

You may have noticed that if you let your mouse drive forward for long enough, it'll start drifting to one side. That's because we're just using open-loop control where we apply some input and hope we get the desired output. For various reasons, including but not limited to the following, our mouse will not drive straight even given the same power to both motors.

* The mouse isn't perfectly balanced as all things should be.
* The ground is not perfectly flat.
* Our motors aren't exactly the same.

To fix this, we'll apply something called closed-loop control. Also known as feedback control, we take measurements from the encoders to adjust the power to our motors and drive straight. For example, if we are veering to the left based on encoder readings, we can increase power to the left motor and decrease power to the right motor to correct it.

One common way to do feedback control is PID. For now, you'll be implementing just the P part of it. Conceptually, feedback controllers try to minimize some error which is the difference between a measured value (aka process variable) and setpoint.

For a P controller, we vary our motor power proportionally to our error. That is, the larger our error, the more power we apply to correct for it.

<p align="center">
    $u(t) = K_pe(t)$
</p>

## Drive Straight

Copy over the skeleton code in [labs/lab5/](../labs/lab5) onto your mouse. Our code is getting too long to just copy paste every time. By default, the code makes the mouse drive forward at 20% speed. Next, copy over your code from [Lab 5](lab5.md) to compute `dist` and `theta` based on encoder readings.

Your job is to apply P control to make the mouse drive straight. The linear velocity doesn't matter too much, just the fact that it doesn't veer left or right. To do this, it would help to answer the following questions.

* What is $\theta$ when driving straight?
* What is the error when driving straight?
* Given an error, how do you change each motor's power to correct for it?

When implementing the P controller, start with $K_p$ values of around 0.1 and tune up and down from there based on performance. To make sure the mouse does move forward, add 0.2 to the `throttle` for each motor in addition to your correction term.

### Checkoff #1

1. Demonstrate your working P controller. Print out your error term too.
2. How do you compute the error term?
3. If we want our applied correction power $u(t)$ to be maximized $(u(t) = 1)$ when the error is 2 radians, what is $K_p$?
4. What happens when $K_p$ is too low? How about too high? What value did you end up using?

## Go the Distance

When solving mazes, it is quite useful to be able to drive forward a set distance. Let's swap out the 0.2 we blindly added to the `throttle` for a linear correction term. Your job is to get your mouse to drive straight forward 200mm and then stop. Like with driving straight, it'd help to answer the following questions.

* What is the error for traveling a set distance?
* Given an error, how do you change each motor's power to correct for it?

When implementing the P controller, start with $K_p$ values of 0.1 and tune. Don't remove your angular correction code from before since we still want to drive straight. Since we want to leave a little wiggle room for the angular correction, limit the linear correction term to around 0.9.

### Checkoff #2

1. Demonstrate your working P controller. Print out your error term too.
2. How do you compute the error term?
3. If we want our applied correction power $u(t)$ to be maximized $(u(t) = 1)$ when the error is 100mm, what is $K_p$?

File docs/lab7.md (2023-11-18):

# Lab 7: More PID

## Background

In the previous lab we were able to get our mice driving a certain distance reasonably straight with just proportional control. This week, we'll learn how to correct for persistent steady state error, turn in place, and follow walls.

Recall our implementation of a **proportional (P) controller** from the last lab.

<p align="center">
    $u(t) = K_pe(t)$
</p>

Proportional control works pretty well for making our mouse drive straight, but you may have noticed a constant offset error. The motors naturally travel at different speeds given the same power and the constant offset error actually accounts for that difference. If we had zero error, we'd actually apply the same power to each motor, generating an error. How might we fix this? What if we kept track of the total error?

<p align="center">
    $u(t) = K_pe(t) + K_i\int_0^t e(\tau) d\tau$
</p>

This is called a **proportional-integral (PI) controller**. The integral keeps track of the total error (both positive and negative) since we first started the controller. Even small errors will cause the integral term to eventually grow large enough and get $u(t)$ to push our mouse back on track.

In order to dampen oscillations and prevent overshoot, we might want to consider the derivative of our error too. This prevents our error from changing too quickly.

<p align="center">
    $u(t) = K_pe(t) + K_i\int_0^t e(\tau) d\tau + K_d\frac{de(t)}{dt}$
</p>

With these three terms, we have our **proportional-integral-derivative (PID) controller**. $K_p$, $K_i$, and $K_d$ are tunable gains that determine the behavior of our error (rise time, peak, overshoot, etc.).

Let's go over what each of the terms in PID means.

* The **P** term (**proportional**) increases our correction proportionally to the error: the higher our error, the more power we should apply to correct for it.
* The **I** term (**integral**) compensates for long-term error and drift by integrating the error over time. While a small tendency for our mouse to veer to the right might have little effect on the P term, it’ll cause the I term to build up until the system reaches the setpoint perfectly.
* The **D** term (**derivative**) takes the derivative of the error with respect to time. Systems often have inertia: the faster our error is already decreasing, the less power we need to apply to correct for it. This dampens our controller and reduces overshooting.

Note this checkpoint has no code.

### Checkoff #1

1. We only have individual measurements of error, not a continuous function. How might we estimate the integral of the error?
2. How might we estimate the derivative of the error?
3. One potential issue with PID control is **integral windup**. You can read about it [here](https://en.wikipedia.org/wiki/Integral_windup). What are some ways of preventing integral windup?

## Turning

Copy over the skeleton code in [labs/lab6/](../labs/lab6) onto your mouse. To encourage code readability, we've added a couple of function definitions that modularize the controller. Adapt your P controller code from [Lab 6](lab6.md) to these functions by filling out the TODOs. If you have a better way of organizing the functions, feel free to change things. Ultimately, it should have the same behavior as Checkoff #2 from Lab 5.

Next, add I and D terms to both your angular and linear P controllers. You may find the `global` or `nonlocal` keywords to be useful for accessing variables defined outside of a function. We highly recommend just tuning the PID constants for your linear controller first and then tuning the angular controller when you implement turning. It's generally easier when that specific controller is being exercised. Good starting values are 10x smaller than $K_p$.

Finally, have your mouse turn 90° in place. This should be as simple as setting a different target $\theta$. For an added challenge, let's create a `turn_left` function which internally loops until the mouse turns about 90° (you choose the threshold for acceptable error) before returning. You may find it useful to be able to reset the odometry back to 0 with the following function.

```python
def reset_odometry():
    lenc.position, renc.position = 0, 0
```

### Checkoff #2

1. Demonstrate your working PID loop driving straight a set distance.
2. Demonstrate your working PID loop turning in place by 90°.
3. Demonstrate turning in place by 90° and then stopping for one second before turning another 90° and so on.
4. Explain your implementation of your integral term. Did you account for integral windup?

## Wall Following

When we're driving in a maze, our mouse will always be slightly misaligned with reference to a wall. Despite driving perfectly straight, this slight error will eventually cause us to crash. By performing feedback control with our IR sensors, we can correct for any misalignment!

In the interest of developing maze solving primitives in the future, you will implement a `forward()` function that will have the mouse drive forwards 180mm and stop. While driving forward, maintain a fixed 45mm distance from a wall on the left.

Optimally, stable wall following means maintaining a 0° angle with respect to the wall. With just one sensor, it's impossible to determine the angle because multiple angles can correspond to the same sensed distance. Performing feedback control on just that sensor works, but it relies on the mouse moving a bit to correct for angular errors. With two sensors, we can determine the angle from the wall based on the difference between the sensors. Wall following could then be implemented as just setting the angle of the mouse based on the distance error and letting its forward motion correct for the distance error.

To implement wall following, start by taking your distance measurement code from lab 3 and your linear and angular PID controllers from the previous checkoff. Conceptually, we want to change the definitions of `theta` and `theta_target` for the angular controller. Based on what was discussed previously, what are the new definitions of `theta` and `theta_target`?

Don't worry about implementing a PID controller for this as a P controller is adequate. Tuning can be a bit tricky. We've found that `Kp_theta=0.01` and `Kp_ang=0.01` work pretty well. Our reference solution uses `Kp_theta` to scale the distance error to set `theta_target`. Since we assume the mouse drives pretty straight and isn't very misaligned, don't worry about tuning your controller to work well for large errors.

### Checkoff #3

1. Demonstrate your wall following code by calling `forward()` once every second.
2. How might you extend your code to drive straight in between two walls?

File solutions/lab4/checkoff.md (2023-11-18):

# Lab 4 Checkoff Solutions

## Checkoff #1

1. Have them manually move the mouse straight and see if the distance roughly matches. Then have them rotate in place and see if the angle matches.

```python
import board
import time
import rotaryio
from math import pi

lenc = rotaryio.IncrementalEncoder(board.GP12, board.GP13)
renc = rotaryio.IncrementalEncoder(board.GP19, board.GP18)

ENCODER_TICKS_PER_REVOLUTION = 217
WHEELBASE_DIAMETER = 78.0 # mm
WHEEL_DIAMETER = 34.0 # mm

while True:
    MM_PER_TICK = pi * WHEEL_DIAMETER / ENCODER_TICKS_PER_REVOLUTION
    left_dist  = lenc.position * MM_PER_TICK
    right_dist = renc.position * MM_PER_TICK

    dist  = (left_dist + right_dist) / 2
    theta = (right_dist - left_dist) / WHEELBASE_DIAMETER

    print(dist, theta)
    time.sleep(0.05)
```

2. About 0.5mm

## Checkoff #2

1. Just needs to be moving at somewhat low speed. Run the code below to get a feel for it. Don't worry about direction. The biggest gotcha is that the IN2 pin needs to be on 75% of the time instead of 25% to get 25% speed.

```python
import board
import pwmio

lmot_in1 = pwmio.PWMOut(board.GP16, frequency=20000)
lmot_in2 = pwmio.PWMOut(board.GP17, frequency=20000)

while True:
    lmot_in1.duty_cycle = 65535
    lmot_in2.duty_cycle = 49151
```

2. Motor direction will reverse.

## Checkoff #3

1. Make sure it does motions specified in the TODOs.

```python
import board
import time
import pwmio
import adafruit_motor.motor as motor

lmot = motor.DCMotor(
    pwmio.PWMOut(board.GP16, frequency=20000),
    pwmio.PWMOut(board.GP17, frequency=20000)
)
rmot = motor.DCMotor(
    pwmio.PWMOut(board.GP15, frequency=20000),
    pwmio.PWMOut(board.GP14, frequency=20000)
)
lmot.decay_mode = motor.SLOW_DECAY
rmot.decay_mode = motor.SLOW_DECAY

while True:
    lmot.throttle, rmot.throttle = 1, 1
    time.sleep(1)
    lmot.throttle, rmot.throttle = 0, 0
    time.sleep(1)
    lmot.throttle, rmot.throttle = -0.25, -0.25
    time.sleep(1)
    lmot.throttle, rmot.throttle = 0, 0
    time.sleep(1)
```

2. It throws an error. Let them know that means we need to keep values within the valid range for future labs.

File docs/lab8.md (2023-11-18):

# Lab 8: Maze Solving Primitives (WIP)

The simplest implementation is to just have `forward`, `turn_left`, `turn_right`, and `turn_around` functions. Turning should be pretty easy, but implementing `forward` is trickier as it needs to wall follow, account for lack of walls to reference, and correct for distance errors. Here's some considerations.

- There are 8 possible cases on wall presence for `forward` bc there are 4 walls in consideration when moving forward one cell.
- If we suddenly see an opening on the left or right (or sudden appearance of a wall) we can correct our internal distance measurement.
- We want to maintain 0° with respect to wall on left and right which means an error for each side. If we see openings on the left and right, the errors will point in opposite directions and we should drive straight using just encoders.
- If we start without a wall on one side, we should wall follow using just the other side. May be a concern if that side suddenly lacks a wall so perhaps just drive straight using encoders.
- Should take the minimum of the efforts to correct for both wall angle errors to account for suddenly seeing an opening on one side.

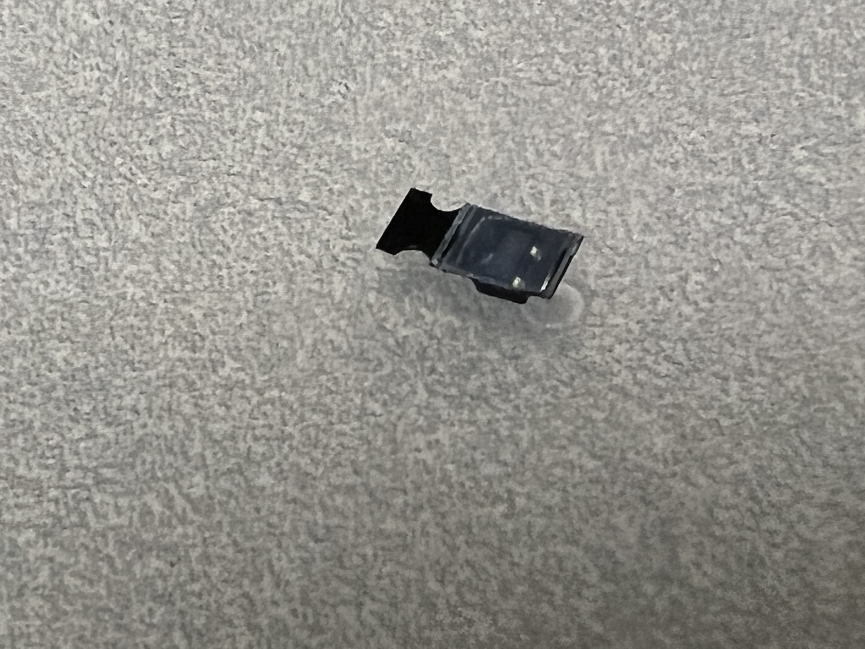
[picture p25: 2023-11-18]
docs/imgs/92AED5EC-55AB-422E-8CC5-3F412DB9CE13.jpeg

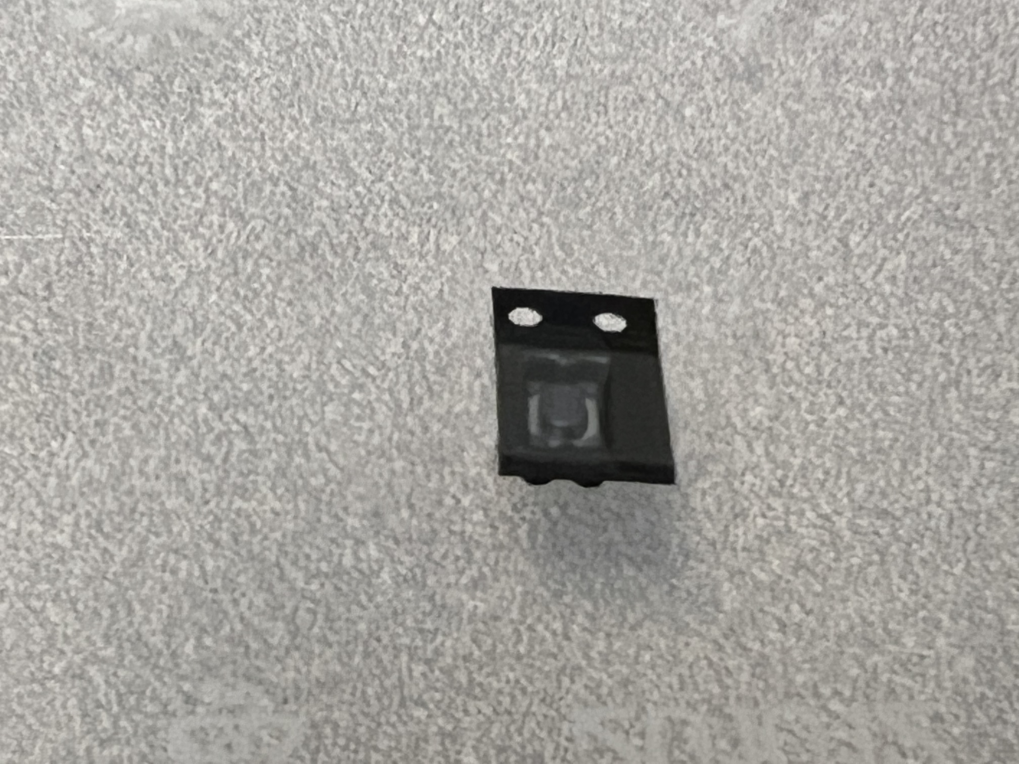
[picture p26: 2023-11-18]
docs/imgs/1DE65BCB-D220-415D-95C7-6C17741371E0.jpeg

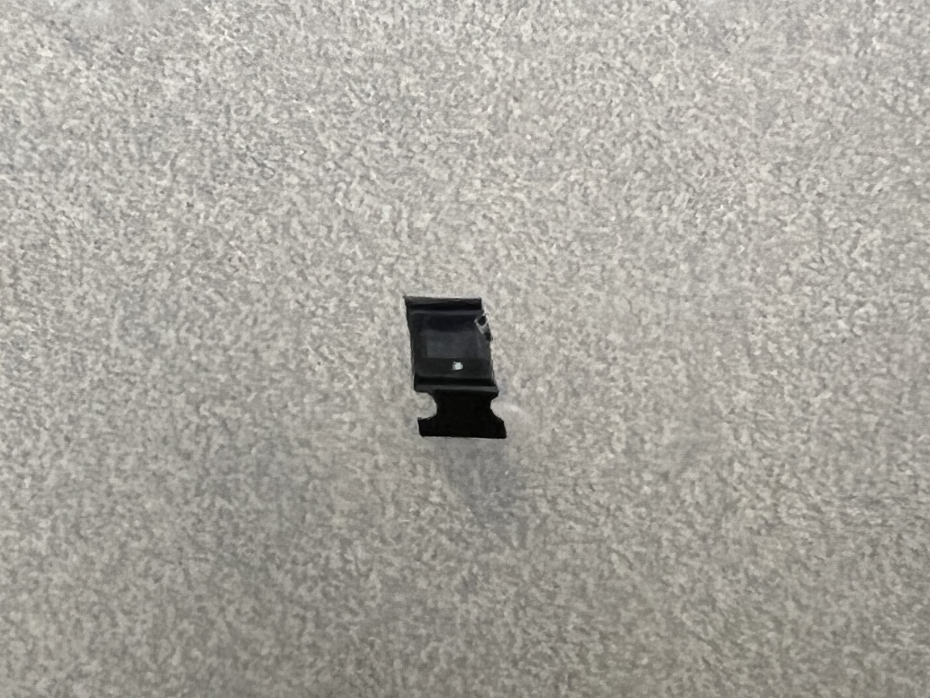
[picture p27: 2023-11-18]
docs/imgs/1DCE4A37-9E28-4FC1-B618-D99F1F2FB529.jpeg

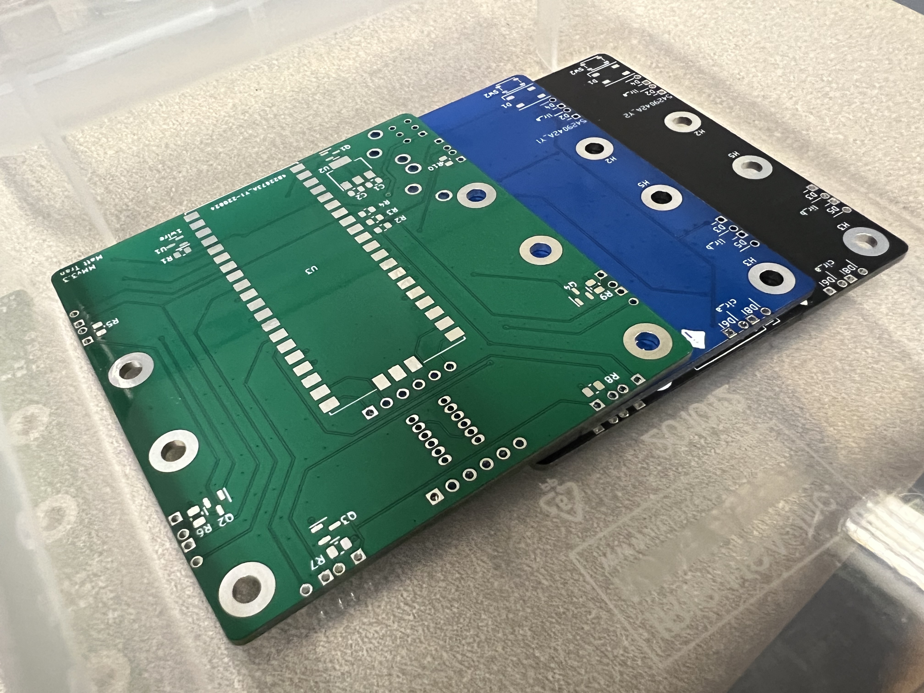
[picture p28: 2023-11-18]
docs/imgs/F96A7274-B9BA-4F07-9B84-48086C9D6B57.jpeg

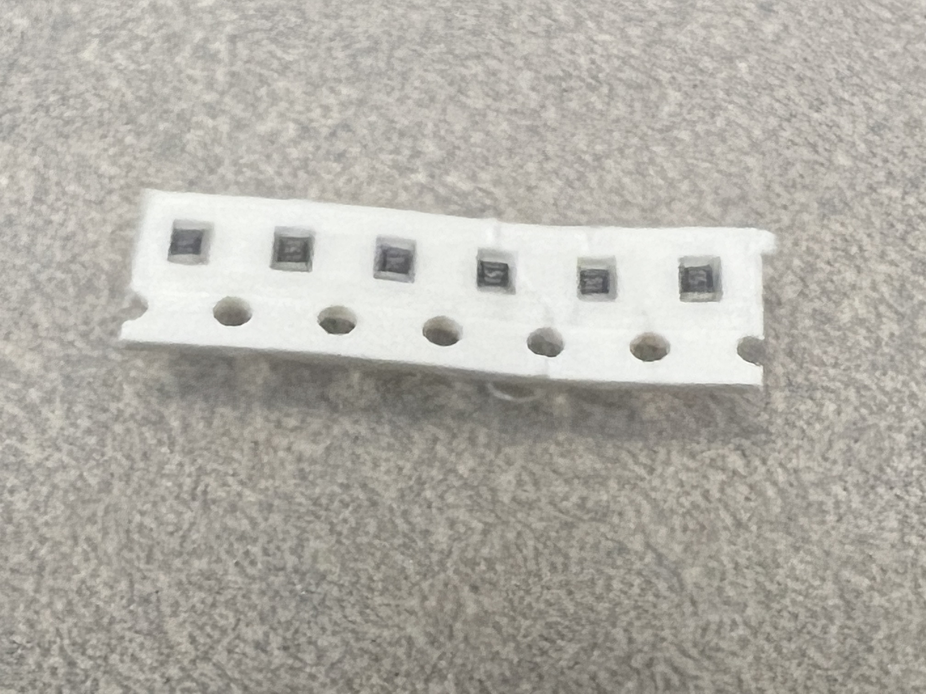
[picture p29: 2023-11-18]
docs/imgs/9D978255-7370-4769-8142-E828E0F5C164.jpeg

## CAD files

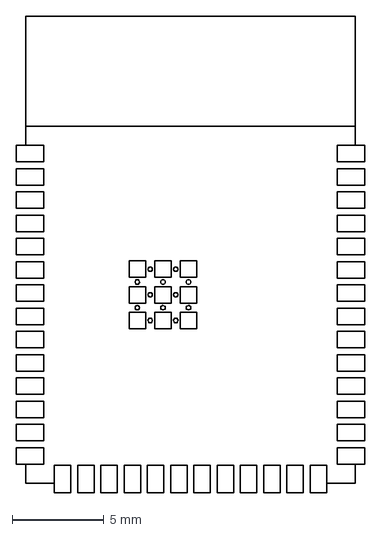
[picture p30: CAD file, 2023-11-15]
PCB/ESP32S3Wroom/ESP32-S3-WROOM-1 PCB Footprint.dxf
19.0 x 26.0 mm

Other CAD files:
PCB/ESP32S3Wroom/boardshape.dwg
PCB/ESP32S3Wroom/ESP32-S3-WROOM-1 PCB Footprint.dwg

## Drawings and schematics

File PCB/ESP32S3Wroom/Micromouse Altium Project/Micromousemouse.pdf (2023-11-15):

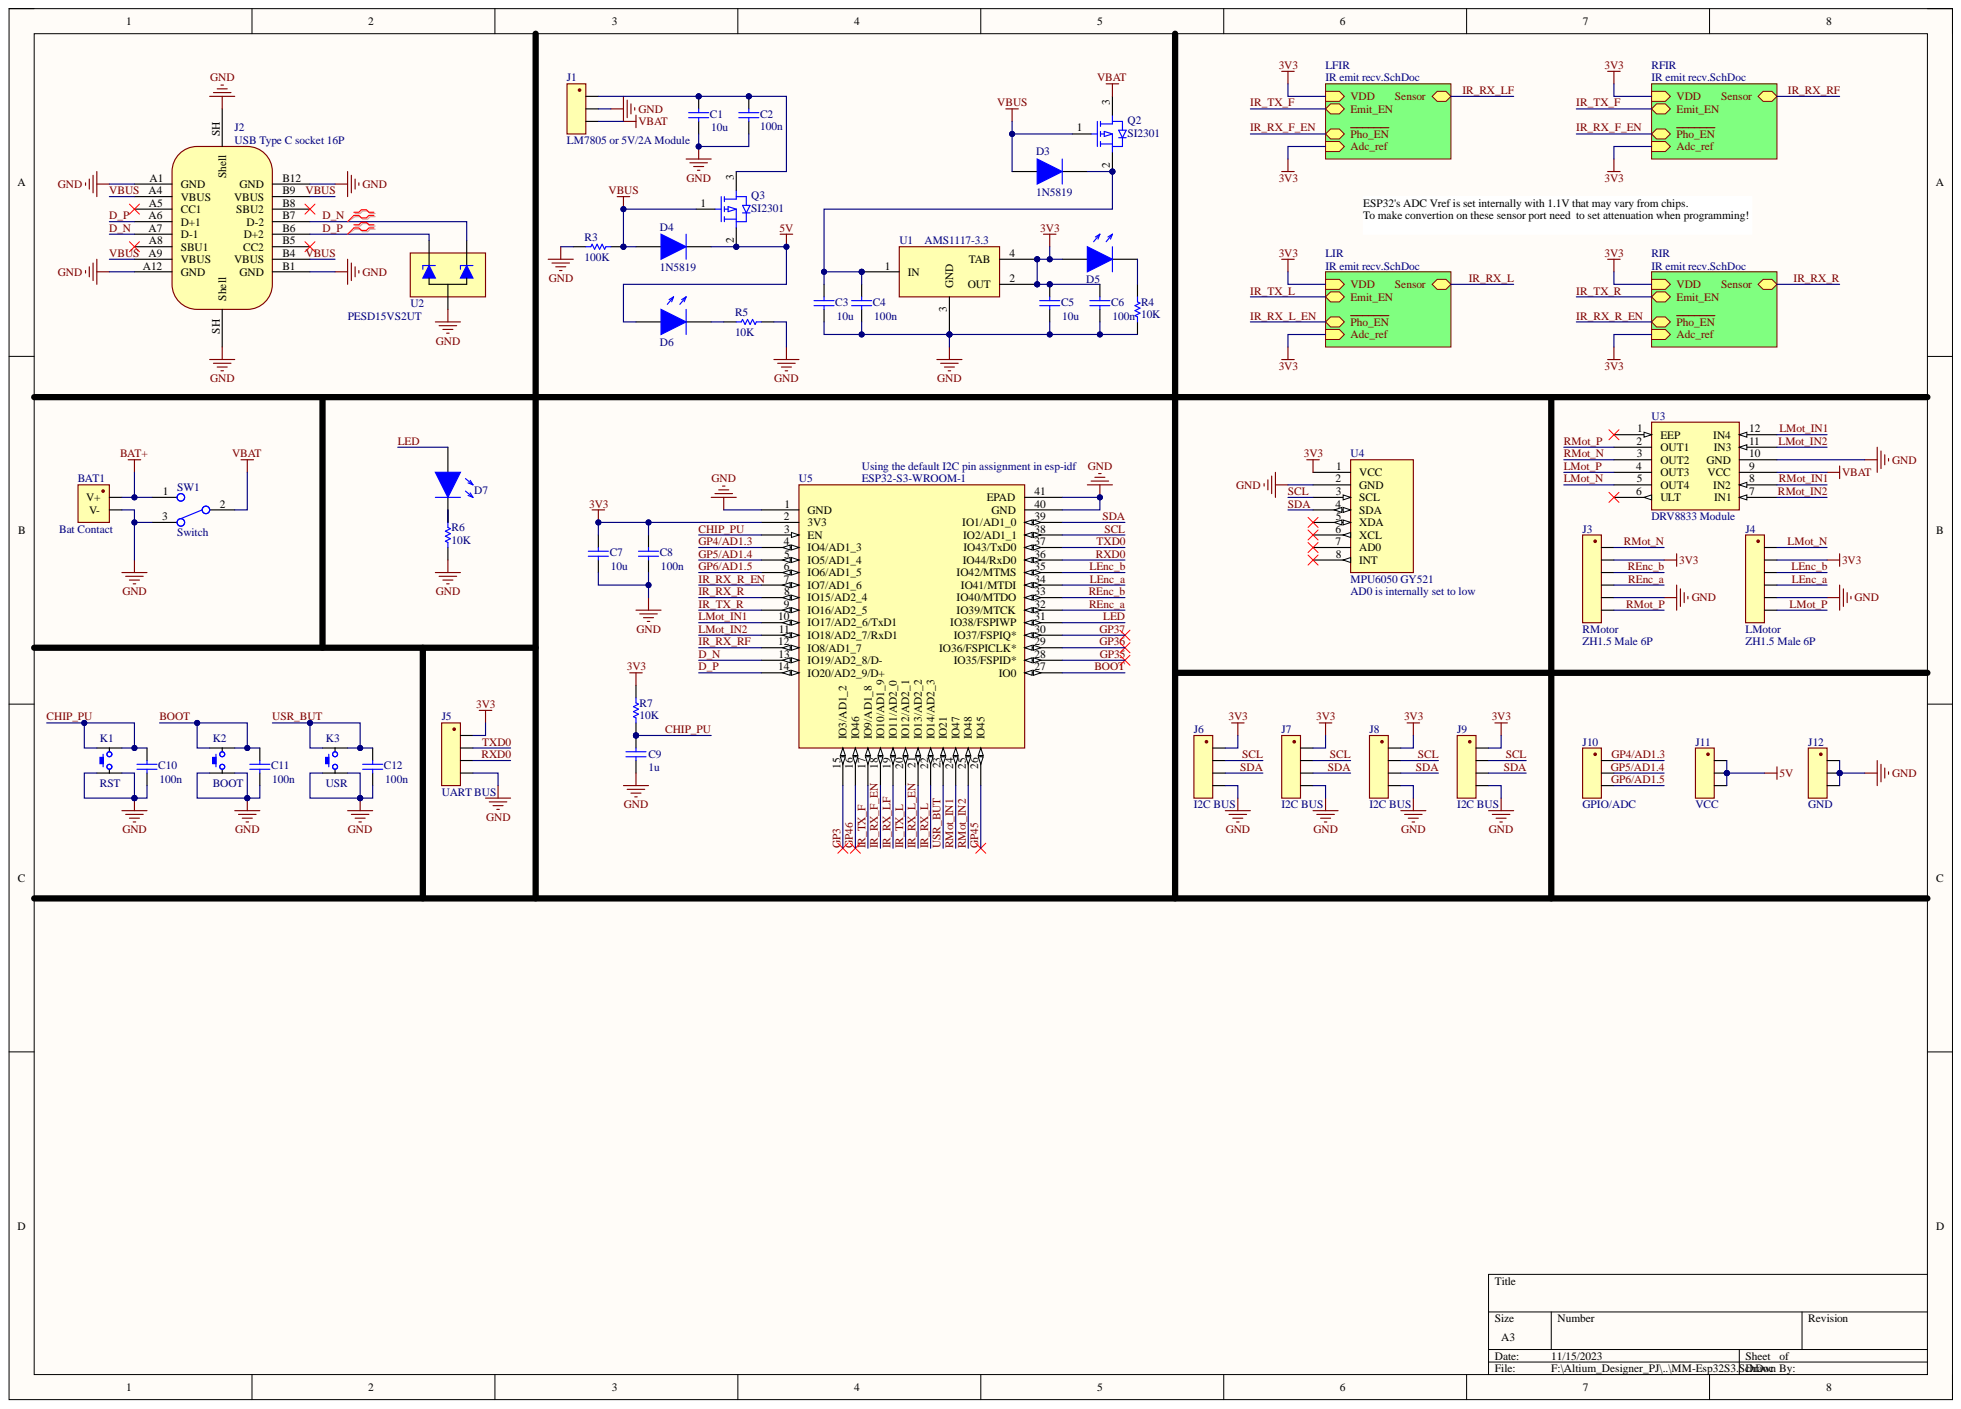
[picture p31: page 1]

ESP32's ADC
To make convertion on these

set internally with 1.1V that may vary from chips

sensor port need to

set attenuation when programming!

LIR
IR emit recv.SchDoc

Using the default I2C pin as
ESP32-S3-WROOM

signment in esp-idf

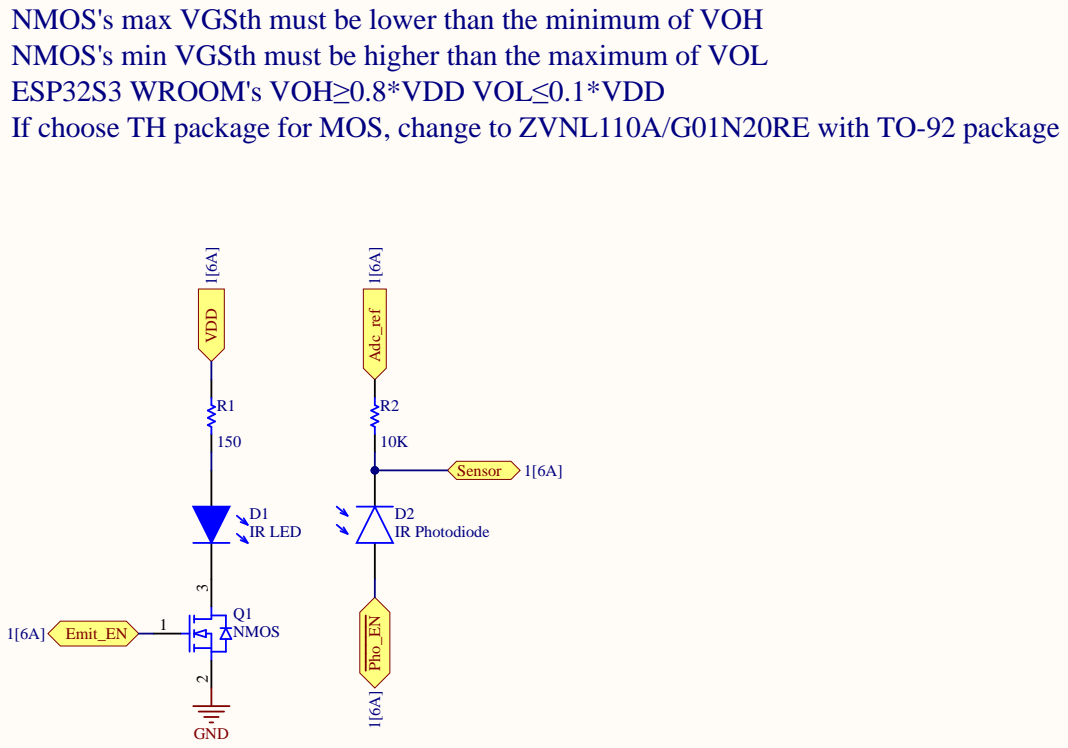
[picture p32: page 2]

NMOS's max VGSth must be lower than the minimum of VOH
NMOS's min VGSth must be higher than the maximum of VOL
ESP32S3 WROOM's VOH
If choose TH package for MOS, change to ZVNL

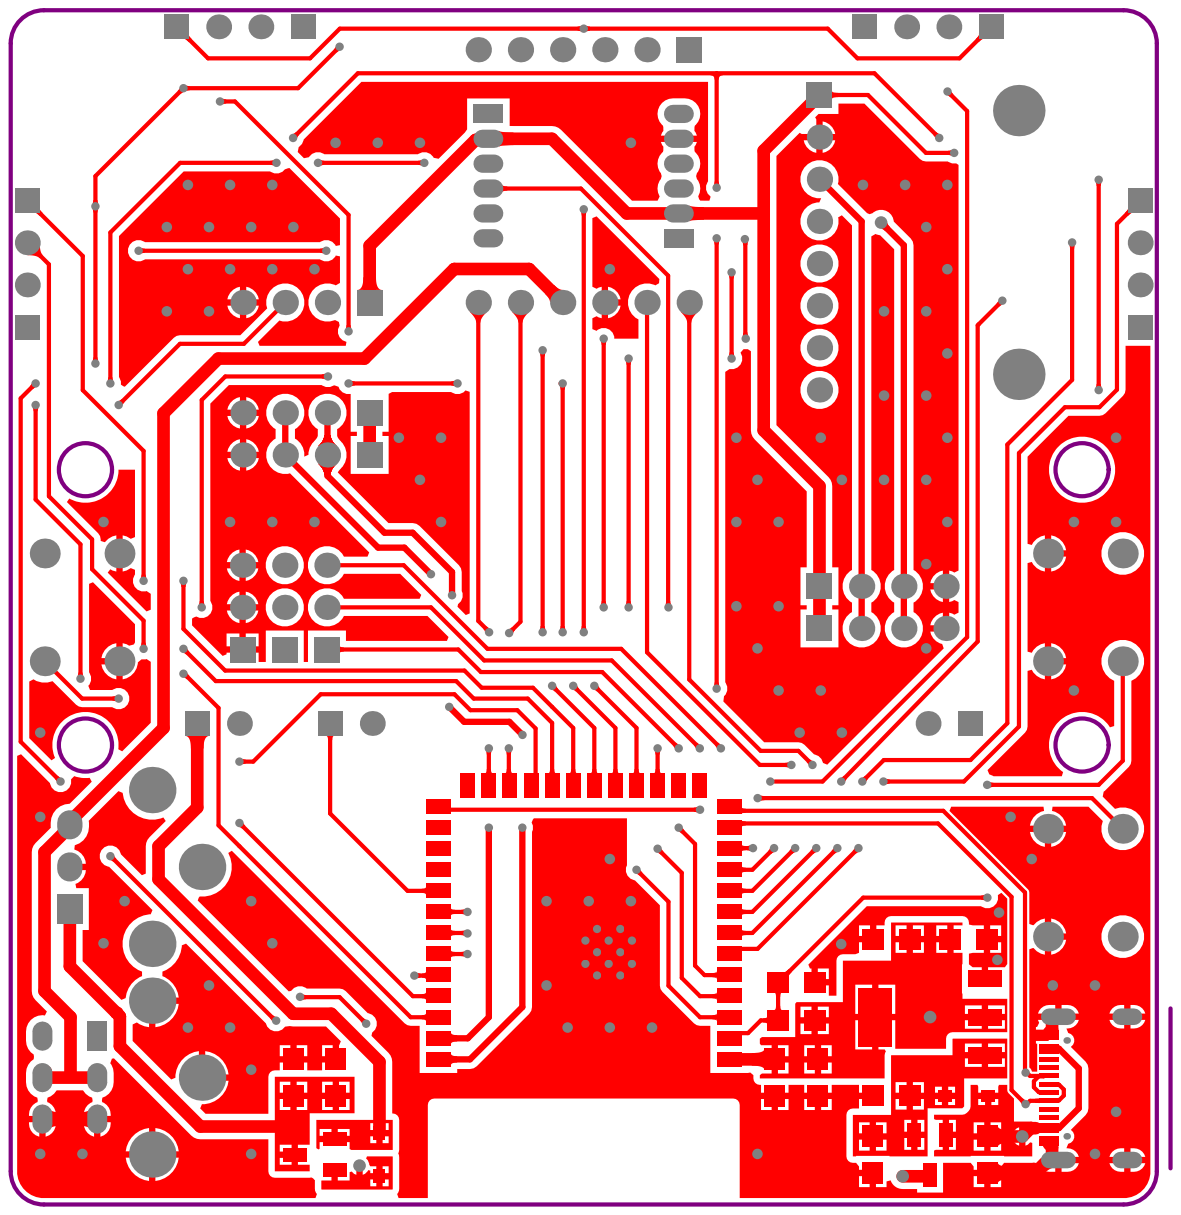
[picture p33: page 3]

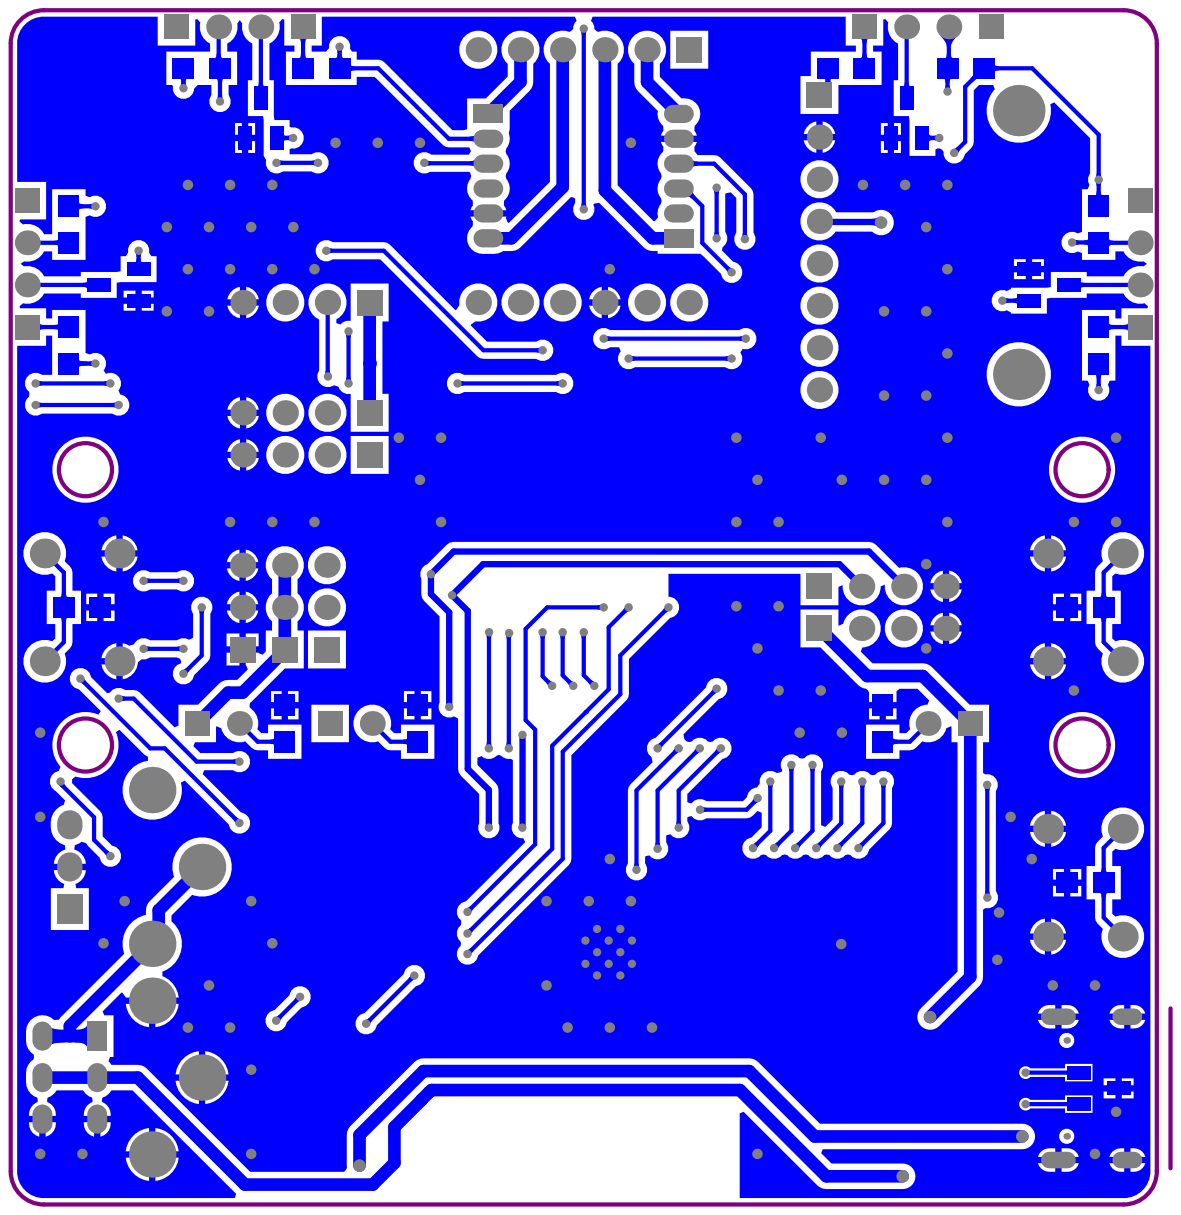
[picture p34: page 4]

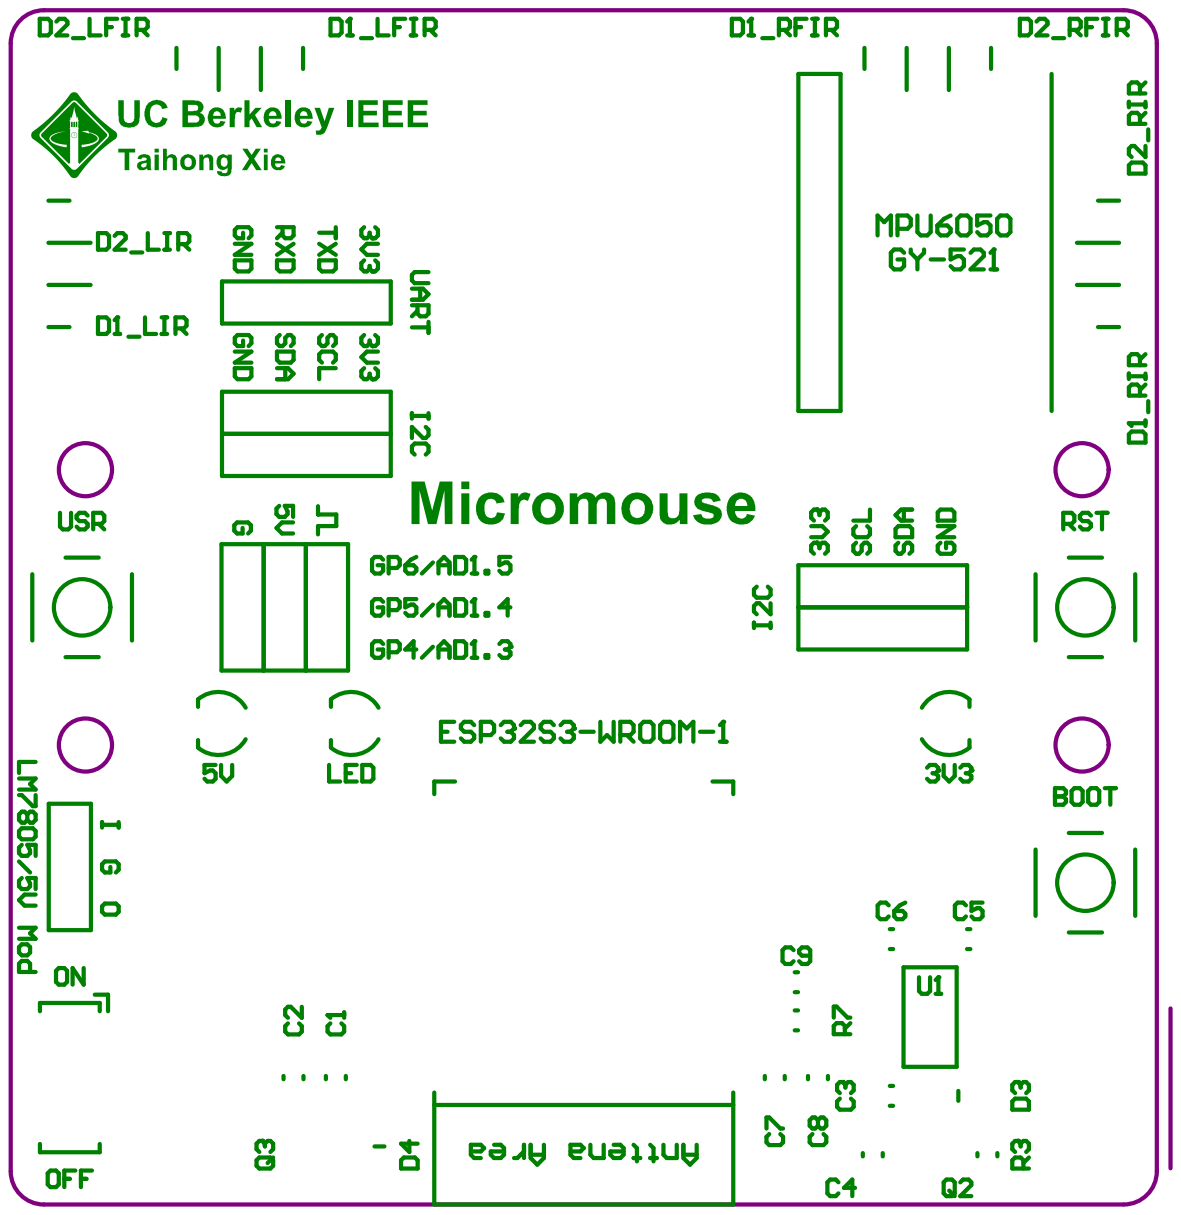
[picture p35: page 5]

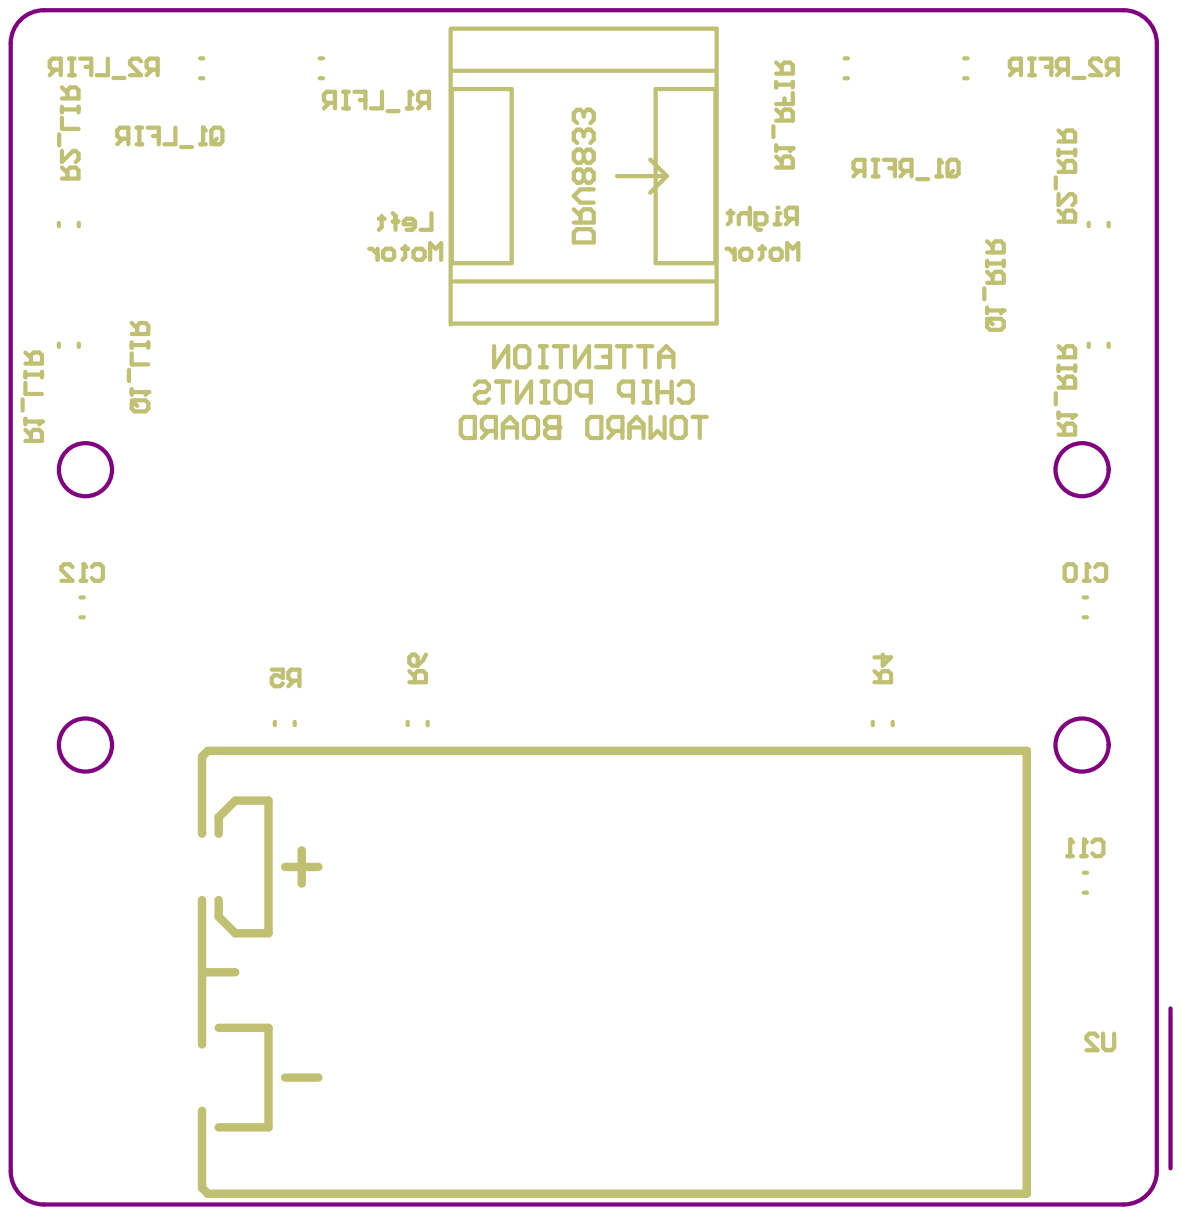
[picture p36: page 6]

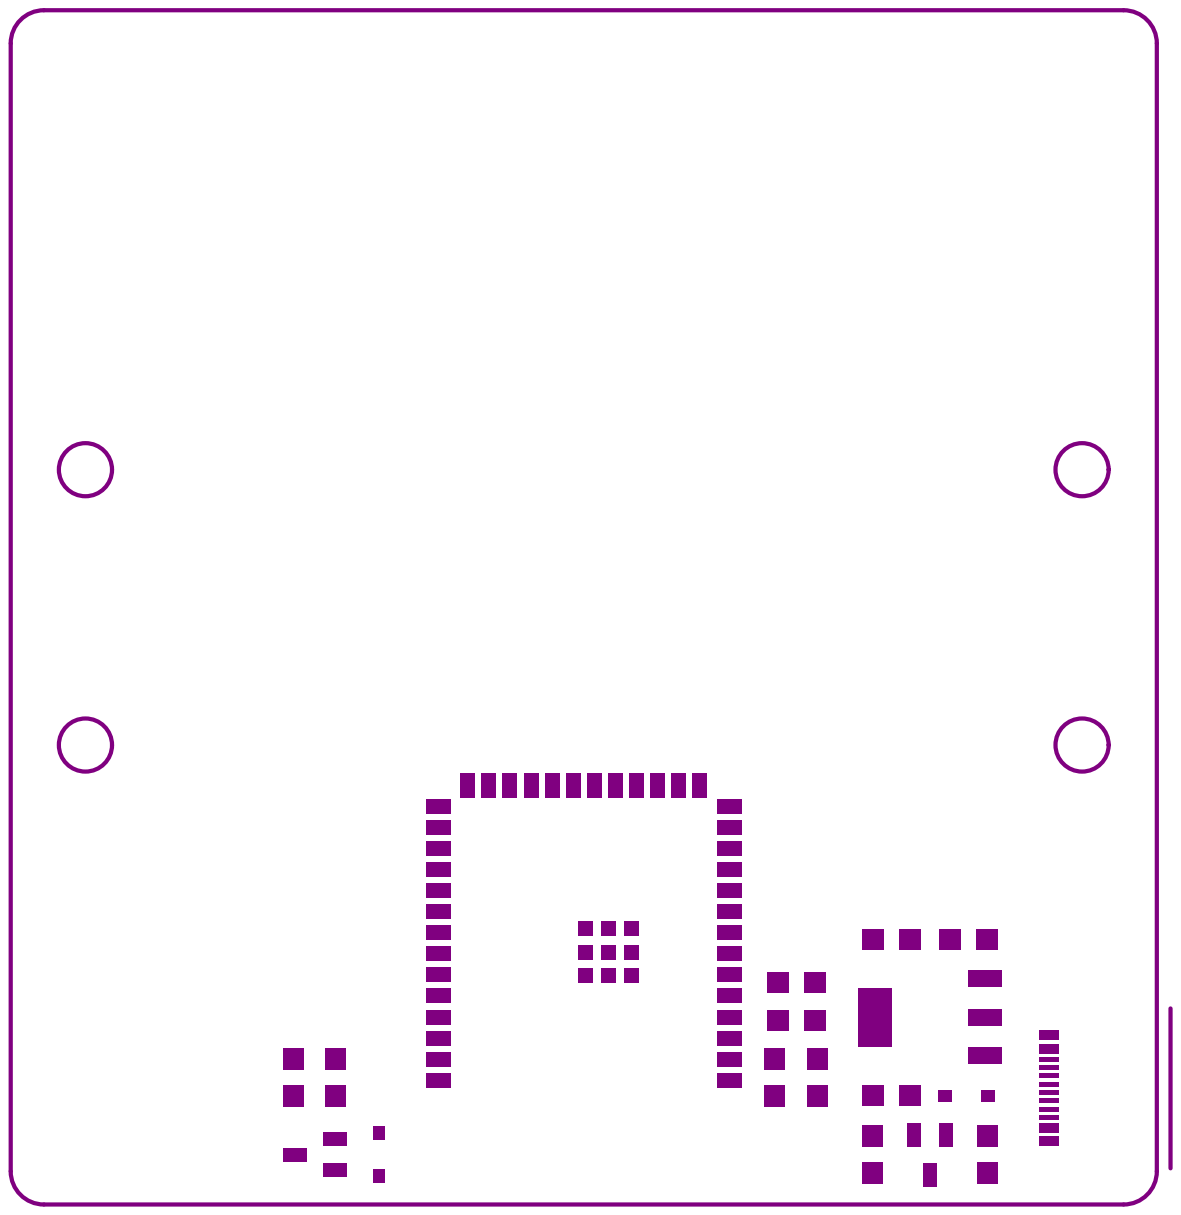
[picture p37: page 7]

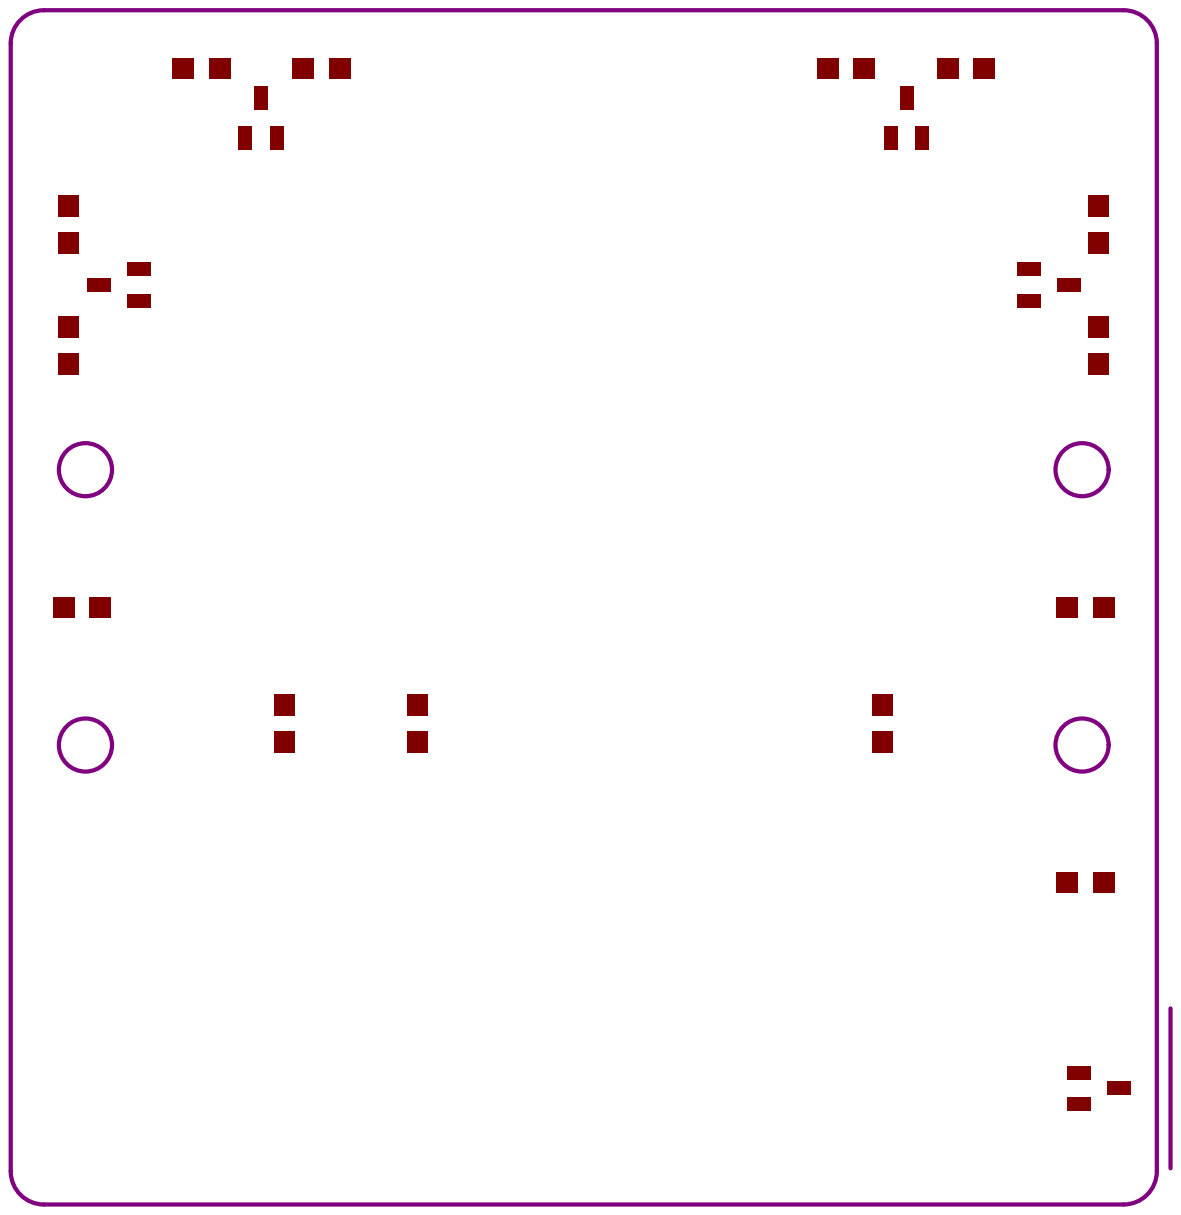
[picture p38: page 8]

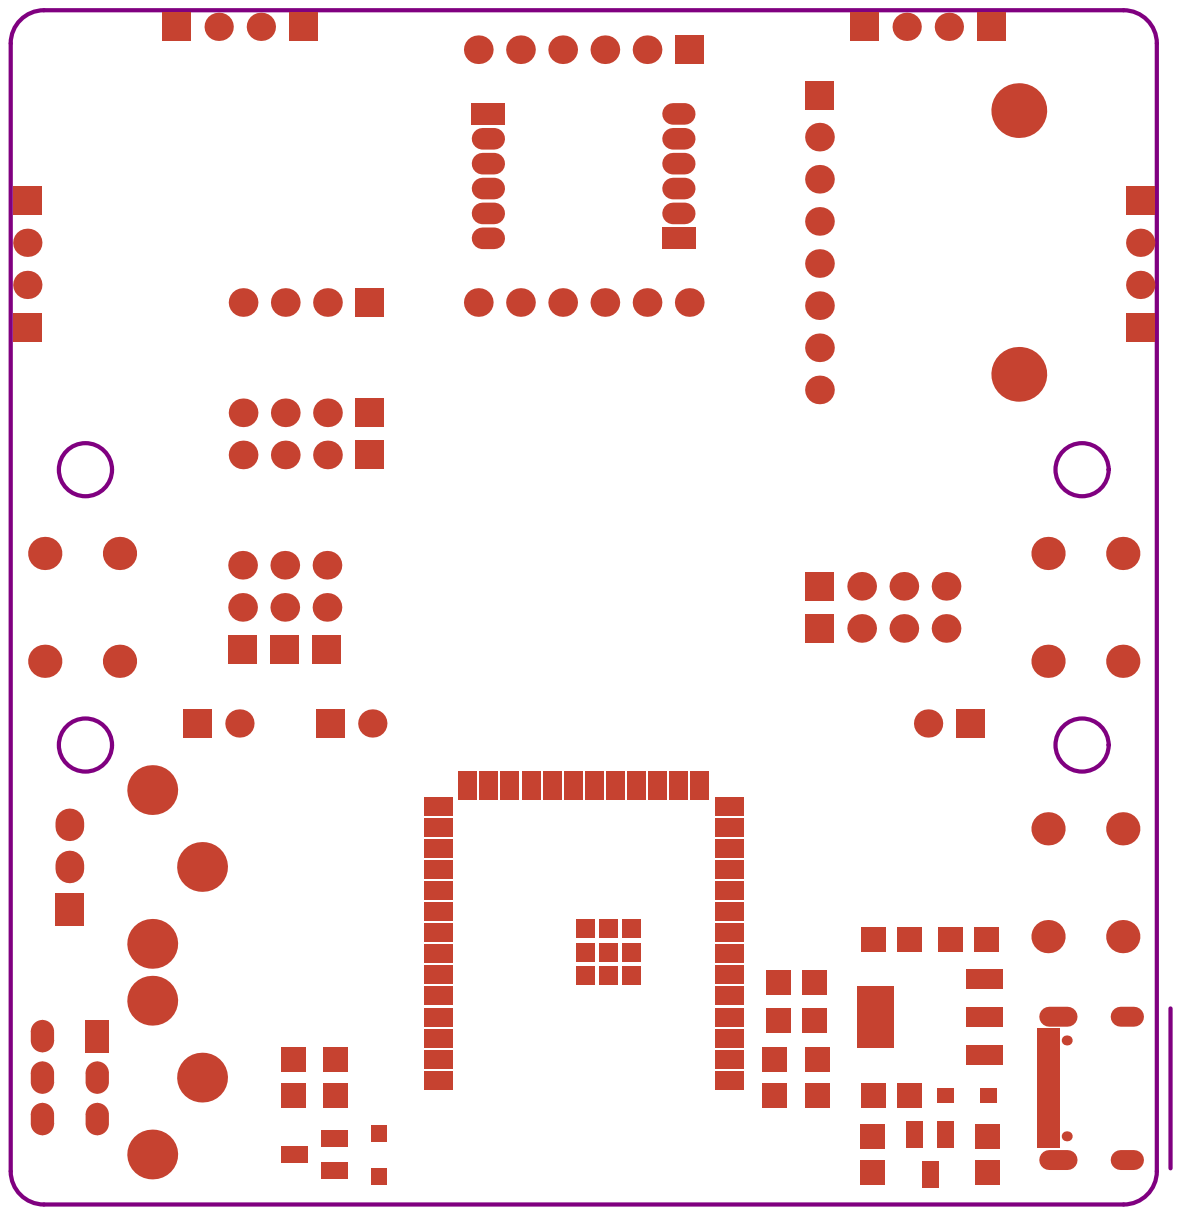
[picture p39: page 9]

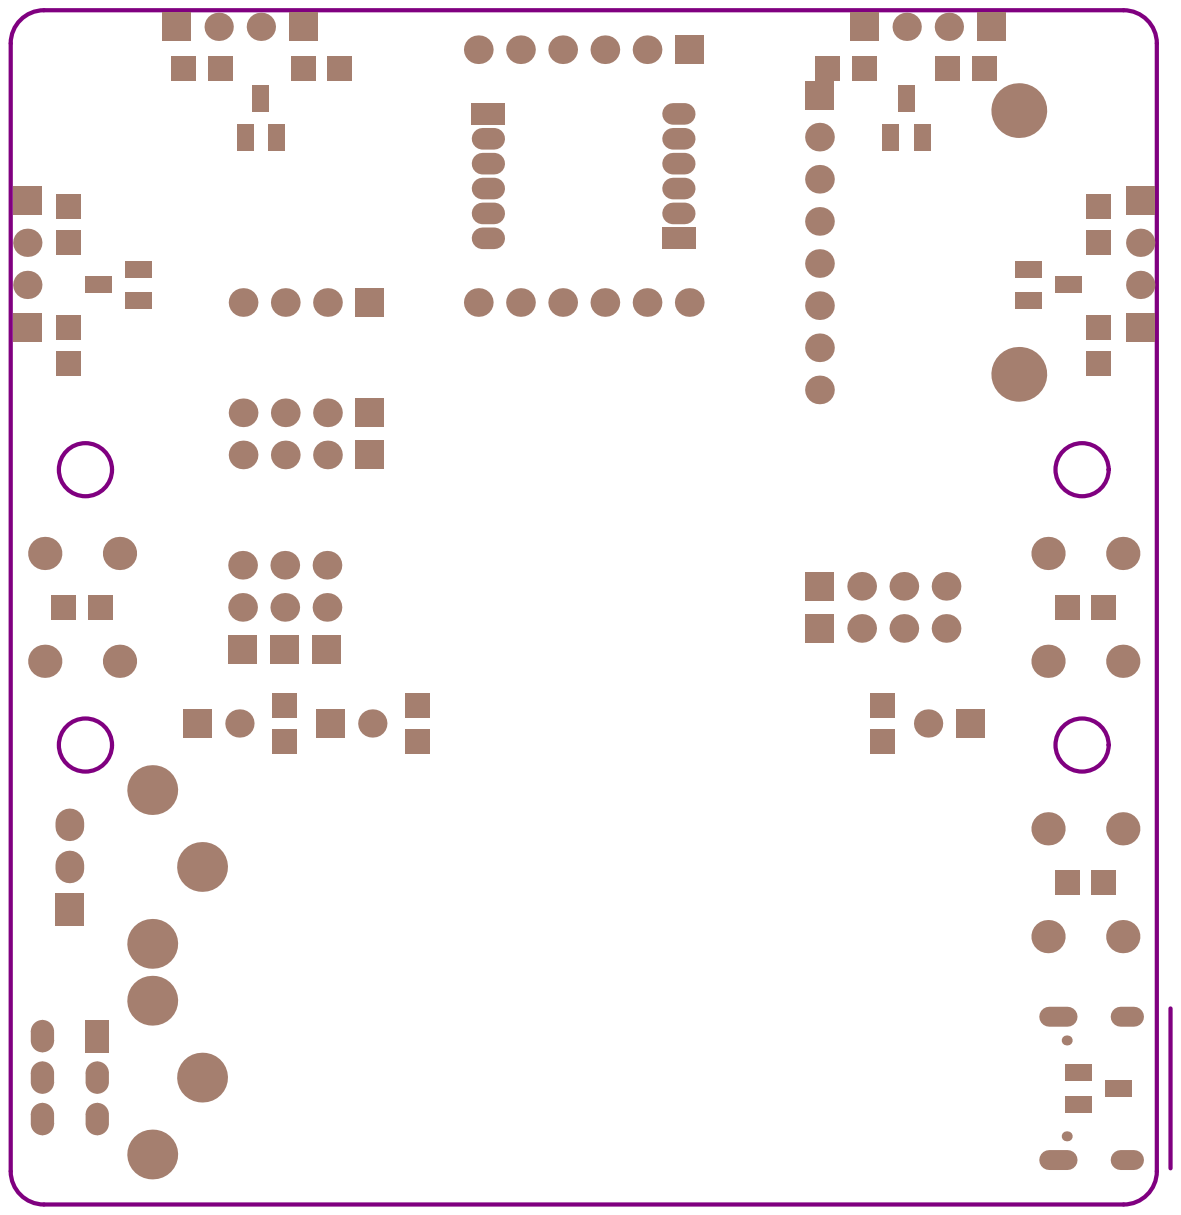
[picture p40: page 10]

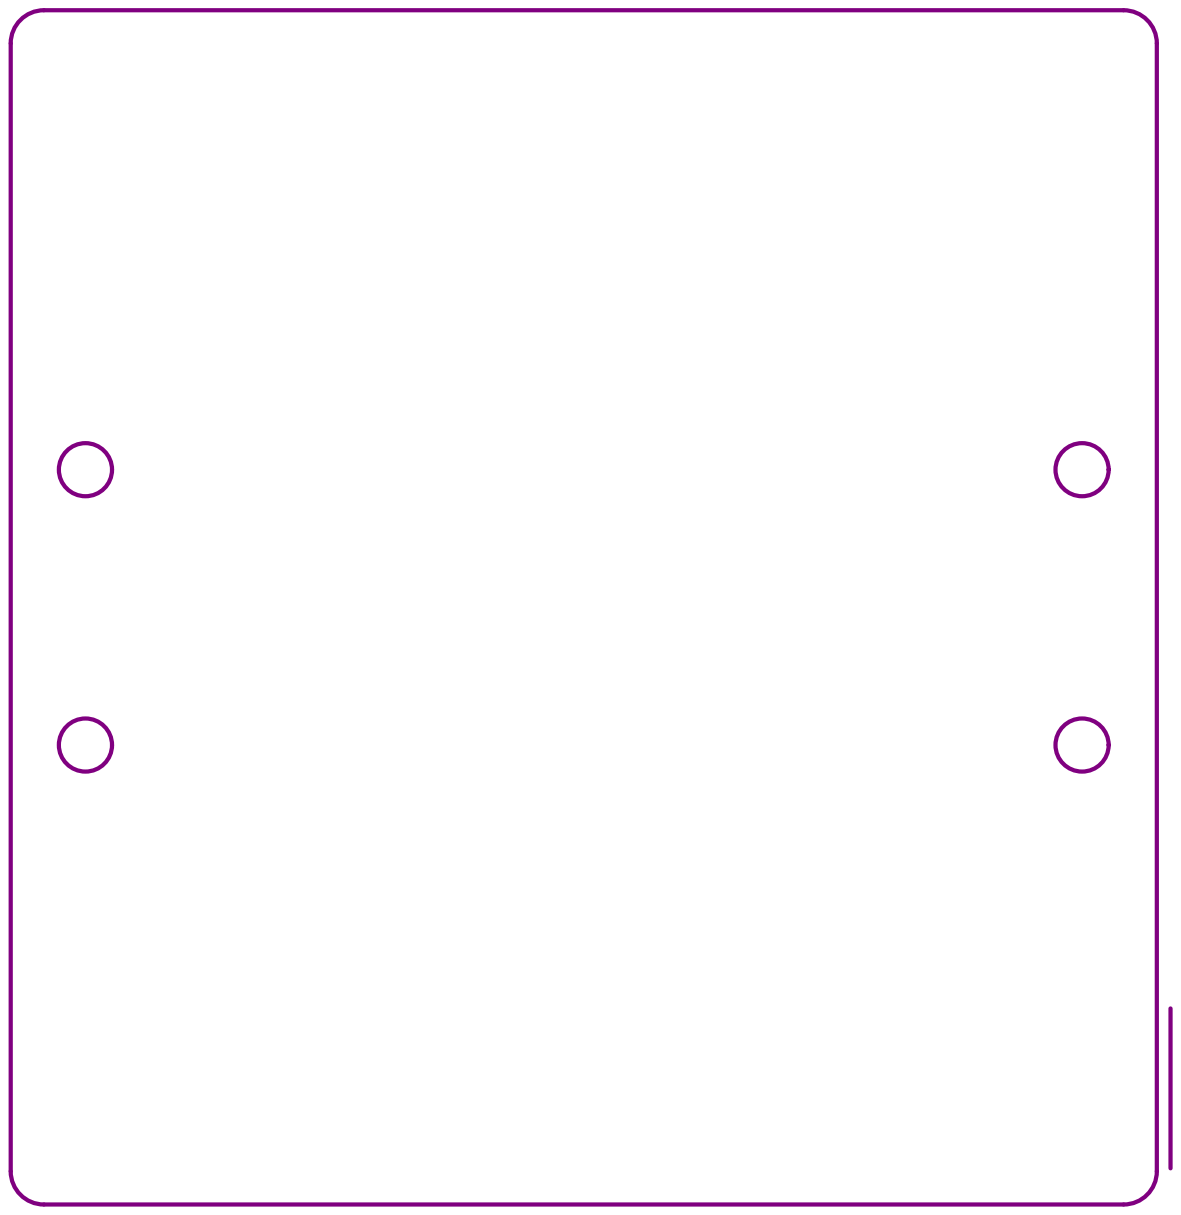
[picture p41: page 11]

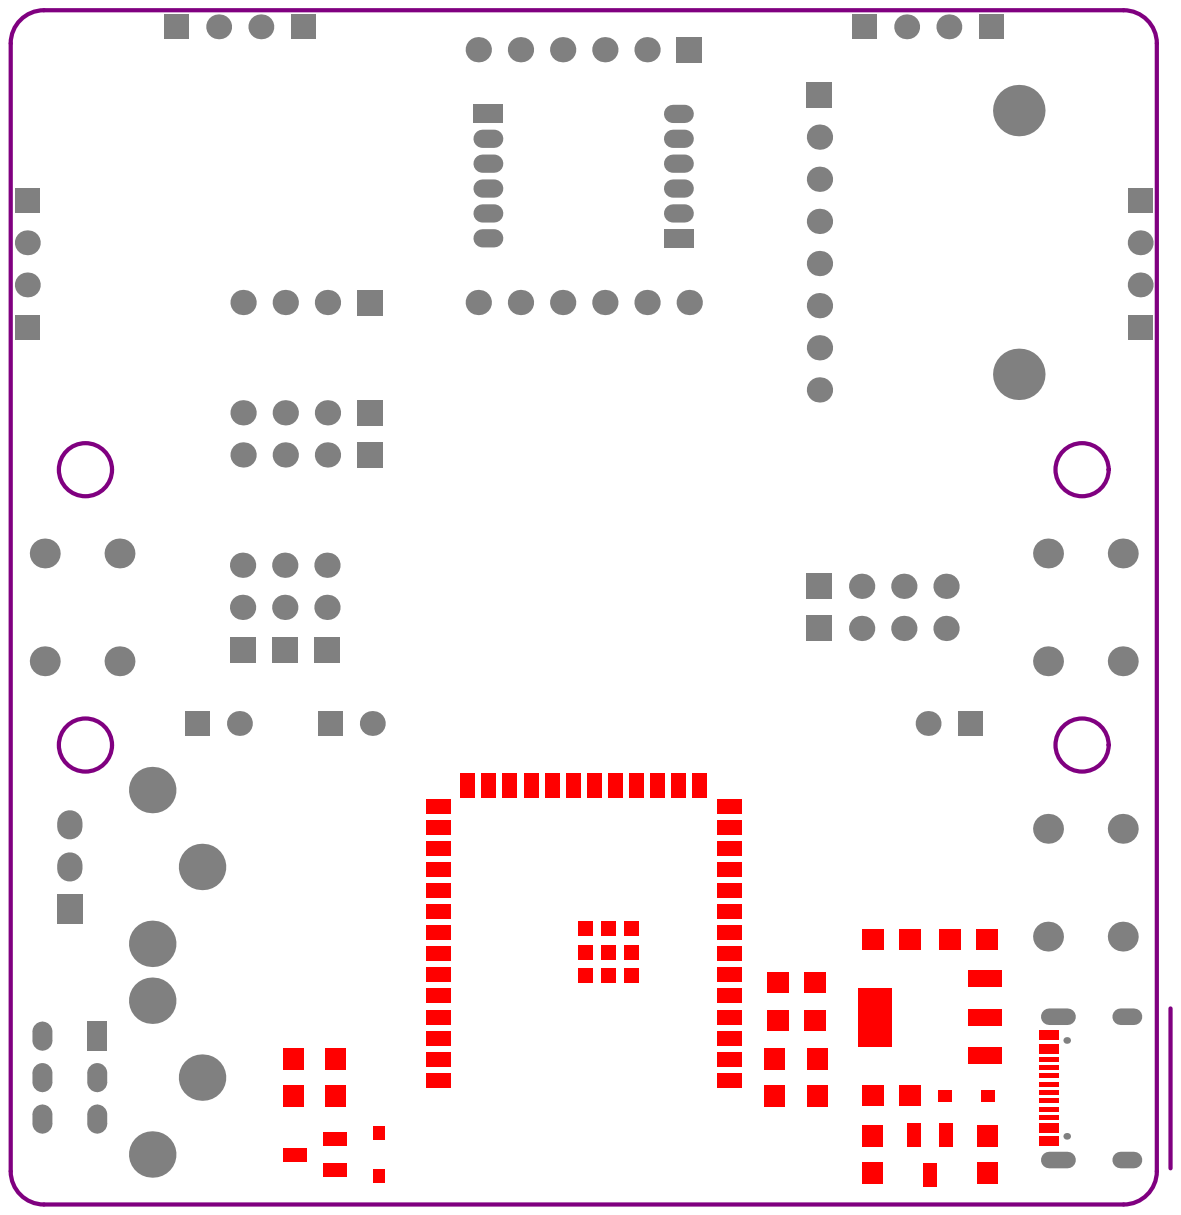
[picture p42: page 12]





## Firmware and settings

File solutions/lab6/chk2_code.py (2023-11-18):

import board
import time
from math import pi

import digitalio
import neopixel
import rotaryio
import pwmio
import adafruit_motor.motor as motor

""" Constants """

ENCODER_TICKS_PER_REVOLUTION = 217
WHEELBASE_DIAMETER = 78.0 # mm
WHEEL_DIAMETER = 34.0 # mm

""" Peripherals """

# debug
led = digitalio.DigitalInOut(board.LED)
led.direction = digitalio.Direction.OUTPUT

but = digitalio.DigitalInOut(board.GP3)
but.pull = digitalio.Pull.UP

rgb = neopixel.NeoPixel(board.GP4, 1)

# encoders
lenc = rotaryio.IncrementalEncoder(board.GP12, board.GP13)
renc = rotaryio.IncrementalEncoder(board.GP19, board.GP18)

# motors
lmot = motor.DCMotor(
    pwmio.PWMOut(board.GP16, frequency=20000),
    pwmio.PWMOut(board.GP17, frequency=20000)
)
rmot = motor.DCMotor(
    pwmio.PWMOut(board.GP15, frequency=20000),
    pwmio.PWMOut(board.GP14, frequency=20000)
)
lmot.decay_mode = motor.SLOW_DECAY
rmot.decay_mode = motor.SLOW_DECAY

""" Main """

def constrain(val, min_val, max_val):
    return min(max_val, max(val, min_val))

# compute dist and theta
def compute_odometry():
    MM_PER_TICK = pi * WHEEL_DIAMETER / ENCODER_TICKS_PER_REVOLUTION

    left_dist  = lenc.position * MM_PER_TICK
    right_dist = renc.position * MM_PER_TICK

    dist  = (left_dist + right_dist) / 2
    theta = (right_dist - left_dist) / WHEELBASE_DIAMETER

    return dist, theta

# compute correction and error terms for a target theta
e_ang_sum, e_ang_prev = 0, 0
def compute_u_ang(theta, theta_target):
    Kp, Ki, Kd = 0.1, 0.005, 0.01

    global e_ang_sum, e_ang_prev
    e_ang = theta_target - theta

    # update I
    e_ang_sum += e_ang
    e_ang_sum = constrain(e_ang_sum, -20, 20) # windup

    # update D
    e_ang_deriv = e_ang - e_ang_prev
    e_ang_prev  = e_ang

    u_ang = Kp * e_ang + Ki * e_ang_sum + Kd * e_ang_deriv
    return u_ang, e_ang

# compute correction and error terms for a target distance
e_lin_sum, e_lin_prev = 0, 0
def compute_u_lin(dist, dist_target):
    Kp, Ki, Kd = 0.01, 0.0005, 0.005

    global e_lin_sum, e_lin_prev
    e_lin = dist_target - dist

    # update I
    e_lin_sum += e_lin
    e_lin_sum = constrain(e_lin_sum, -100, 100) # windup

    # update D
    e_lin_deriv = e_lin - e_lin_prev
    e_lin_prev  = e_lin

    u_lin= Kp * e_lin + Ki * e_lin_sum + Kd * e_lin_deriv
    u_lin = constrain(u_lin, -0.3, 0.3)
    return u_lin, e_lin

def run_control_loop(theta_target, dist_target):
    dist, theta = compute_odometry()
    u_ang, e_ang = compute_u_ang(theta, theta_target)
    u_lin, e_lin = compute_u_lin(dist, dist_target)
    lmot.throttle = constrain(u_lin - u_ang, -1, 1)
    rmot.throttle = constrain(u_lin + u_ang, -1, 1)
    return e_ang, e_lin

def reset_odometry():
    lenc.position, renc.position = 0, 0

def reset_controls():
    global e_ang_sum, e_ang_prev, e_lin_sum, e_lin_prev
    e_ang_sum, e_ang_prev, e_lin_sum, e_lin_prev = 0, 0, 0, 0

def turn_left():
    reset_odometry()
    while abs(run_control_loop(pi/2, 0)[0]) > 0.05:
        time.sleep(0.02)
    reset_controls()
    lmot.throttle, rmot.throttle = 0, 0

if __name__ == "__main__":
    while True:
        turn_left()
        time.sleep(1)

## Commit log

2023-10-01 project created
    [MMV4.kicad_pcb, MMV4.kicad_sch]
2023-10-01 library for esp32
2023-10-09 switch to AD
    [MMV4.kicad_pcb, MMV4.kicad_sch]
